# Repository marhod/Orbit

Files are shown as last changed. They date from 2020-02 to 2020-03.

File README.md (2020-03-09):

# Project Orbit, a 3D Printed Record Player

## This project is designed to be a PROOF OF CONCEPT for a 3D Printed Record Player.

### It is intended to:
* Act as a thought experiment applying modern fabrication techniques to a vintage application.
* Be a cool use of 3D Printing
* Act as a proof of concept
* Play records
* Make people say "Hey's that's cool!"
* Have some fun 3D Printing
* Maybe give some people a new lease on some crappy records from a thrift store

### It is NOT intended to do any of the following:
* Replace a manufactured turntable
* Have exceptional sound quality
* Be a perfect implementation of a design or project
* Be even a good quality turntable.  Are you kidding me?

### A quick and dirty FAQ

#### Q: This is the worst turntable ever.  You're a horrible human being.
A: ... Seriously?   It's a fricking 3D Printed record player.  If it's not cool enough, go design your own before criticising me.  When you do, ping me, because I'll tell you it's fucking awesome and want to buy you a beer.

#### Q: Why did you pick this motor?
A: I wanted something super cheap and off the shelf.  It had to be cheap, have enough torque, and be controlled with 12v.   Yes, it's noisy, but this is a proof of concept and I can source a better motor later.

#### Q: Why did you use Direct Drive?
A: I actually did the first version with belt drive, but the maths for pulley ratio and centers gets annoying when you are testing lots of different motors, which I did.

#### Q: Why did you hotglue on a cartridge?
A: This is a super cheap cartridge.  I got 3 for $10 delivered.  And frankly, using hotglue connector for this level of quality of a device is not a big deal.  Yes, it might be misaligned, but it's an experiment!  

#### Q: Why did you use a ceramic cartridge?
A: It's cheap!

#### Q: The platter wobbles.  
A: Yep it does.  I'm unsure why this happens, but my guess is it's to do with the Z axis on printers being not terribly accurate.  If it is out of plumb by even 0.1 degree that would translate to a 300mm platter wobble of 0.5 millimeter. 

#### Q: I saw the video and your beard is glorious, how can I have one?
A: Don't shave for a bit.  Then after you do that, rub it against a bee hive, ignoring the hundreds of stings from angry bees, until sufficient wax is in the beard, then mould and comb the bear into shape.  Or use product, whichever is easier.

#### Q: How can I align the cartridge?
A: Buy a better quality cartridge, then you can.  The tone arm has slots at the standard distances for a cartridge, but frankly, you have other problems that need to be solved before spending cash on a good cartridge for this device!

#### Q: How do you sleep at night?
A: On a bed filled with shattered dreams, unused parts and broken records.  But I have your mom to keep me company, so there is that...

#### Q: I saw it on Youtube and it sounds terrible 
A: It's a proof of concept made from off the shelf parts and 3D Printing.  How are you not getting this?  

## A quick note

This is a cool project and a bit of a lark.  Don't take it too seriously.

If you're looking for great sound, go spend a few thousand on a good turntable (I have).  If you're looking for a fun experiment, keep reading... :)  It's shoddily made, won't sound amazing, but I guantee your friends will say "WOAH THAT IS COOL" if you make one.  Don't put your expensive records on it, it's a fun project that may damage them.  

This project is not for beginners.  It implies a basic knowledge of electronics, arduino and sufficient skills to be able to 3D Print the parts.  All of these parts can be substituted, and hacking this to make it better is strongly encouraged.

## Parts List.

* All the STL files in this github.
* 1x 12VDc 36 RPM Geared Motor - https://www.ebay.com.au/i/254510260087?itemid=254510260087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
* 1x 2.1mm Barrel Socket - https://www.jaycar.com.au/2-1mm-bulkhead-male-dc-power-connector/p/PS0522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
* 1x 2.1mm Barrel Jack - https://www.jaycar.com.au/2-1mm-dc-power-line-connector/p/PP0509
* 1x Arduino Uno - https://www.amazon.com.au/ELEGOO-Board-ATmega328P-ATMEGA16U2-Arduino/dp/B01EWOE0UU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
* 1x Adafruit Motor Shield - https://www.adafruit.com/product/1438
* 1x Record Player Cartridge - https://www.ebay.com.au/itm/Turntable-Phono-Ceramic-Cartridge-with-Stylus-Needle-for-Vinyl-Record-Player-FS/192885929313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
* 1x 4 pack of Headshell Wires - https://www.ebay.com.au/itm/Turntable-Record-Player-Cartridge-Tonearm-Headshell-Leads-Wires-x-4-Tin-Plated/153731922565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
* 1x Illuminated Momentary Switch - https://www.ebay.com.au/itm/4-Pin-12V-12mm-Angel-Eye-LED-Light-Metal-Push-Button-Momentary-Switch-Waterproof/311981318686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
* 2x RCA Panel Mount Sockets - https://www.ebay.com.au/itm/Panel-Mount-RCA-Female-Socket-Connectors-Adapters-x-2-Pcs/273392016355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
* Thin gauge wire, a ribbon cable is perfect.
* 4x M5x16mm screw
* 1x M5x65mm Screw
* 5x M5 Nut
* 8x M3x8mm screw
* 2x M3x15/16mm screw
* 2x M3x8 Nut
* 1x M3x25mm Screw

## Basic Instruction.  I mean Basic.  Read between the lines until I publish some pictures.  This isn't instructibles.

1.  Print files.    Print the following in whatever you usually print in with PLA.  I used 10% infill and no supports or rafts.  There is one file that must be printed with 100% infill and it's clearly identified.   Choose whichever sizes you can fit on your printer, the bigger the better, but honestly, just print whatever works for you.
2.  Flash the Arduino with the .INO code provided.
3.  Attach the motor to the Motor Carrier with 2x M3x8mm screws.  Do not overtighten.  Just tight enough to be secure.
4.  Attach the Motor Carrier to the Chassis with 2x M3x8mm screws.  
5.  If you printed a two piece chassis due to a small printer, connect the two pieces with 4x M5x16mm screws and nuts.
6.  Hot glue your Cartridge (Record player needle) to the Tone Arm.
7.  Feed your thin gauge wires up through the tonearm.  
8.  Strip one end of the headshell wires, and solder the stripped end to the thin gauge wires.
9.  Connect these to the cartridge.  Take note of the pins and colors.
10.  Feed these through the hole on the chassis.
11.  Feed Attach them to the RCA jacks as per this image: https://www.turntableneedles.com/Images/CartWiring.gif
12.  Solder the 2.1mm Barrel Jack to the 2.1mm Barrel Connector with a short length of wire.
13.  Attach the Arduino with 4x M3x8mm Screws.
14.  Connect it up to the chassis, and plug the arduino into it.
15.  Time to solder the switch, do one end first, then feed it through the hole on the front of the panel, otherwise you wont be able to connect it.
16.  Thread a resistor between the - pin on the button and the GND pin on the button.
17.  Solder Pin 5 on the motor shield to the + pin on the button, using ribbon cable
18.  Solder GND on the motor shield to the - pin on the button, using ribbon cable.  
19.  Solder Pin 6 on the motor shield to one of the remaining pin that DOES NOT have a resistor., using ribbon cable.
20.  Solder GND on the motor shield to the last pin, the one that DOES have the resistor, using ribbon cable.
21.  Attach the Tone Arm Pillar to the Chassis with a M3x15mm screw.
22.  Attach the Tone Arm Bearing to the Tone Arm Pillar with a M3x8mm screw (must be loose)
23.  Attach the Tone Arm Rest to the Chassis with a M3x15mm screw.
24.  Attach the Tone Arm Rest Clip to the Tone Arm Rest with a M3x8mm screw.
25.  Attach the Hub to the Motor Spindle.  Align the flat spot with the screw hole, and insert a M3x25mm screw to act as a set screw.
26.  Push the Platter down onto the Spindle.
27.  Attach the Tone Arm to the Tone Arm Bearing using 2x M3x8mm screws (one on each side) or 1x M3x25mm screw all the way through.
28.  Plug in a 12VDC Power Supply, Sacrifice a Goat, Press the power button.
29.  Play music.

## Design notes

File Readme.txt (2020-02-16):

Print the following in whatever you usually print in with PLA.  I used 10% infill and no supports or rafts.

Hub
Motor Carrier
Tone Arm Bearing
Tone Arm Pillar
Tone Arm Rest Clip
Tone Arm Rest

Print the following in something light.  PLA is probably fine, but carbon would be cool.  You can find it in "Print in Carbon or Light Material"

Tone Arm

Print the following with 100% infill.  You can find this part in the "Print with 100% infill"

Tone Arm Weight

If you have a large volume printer (300x300mm or larger) you may be able to print the body and 300mm platter in single pieces.  These pieces can be found in "Parts for Large Build Volume".  PRINT UPSIDE DOWN FOR BEST QUALITY.

300mm Platter
Body

If you have a small volume printer (260x260mm or smaller) you will need to print these the split and smaller versions of these parts.  These can be found in the "Parts for small build volume".  Print the largest platter you can fit on your printer.    
220 / 260mm Platter
Left Hand Body
Right Hand Body

Lastly - if you want to do something cool and put a logo on the machine, I'd do it on the platter.  We could emboss it into the platter, but this may cause weight / balance issues.  A better solution would be to use a multi-material printer to paint or print it with your logo on the platter.  I don't know how to do that... :)

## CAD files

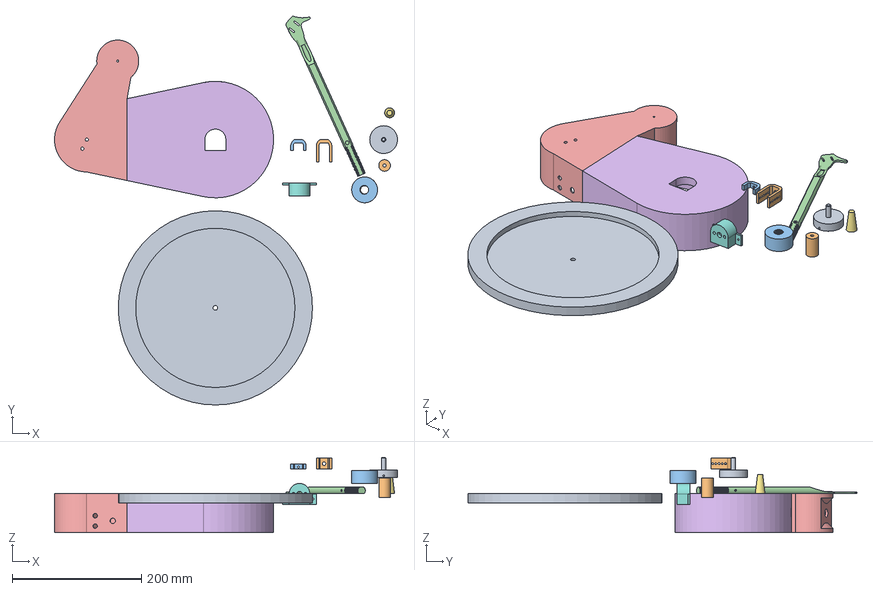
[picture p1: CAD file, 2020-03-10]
Orbit v2.step
530.0 x 600.9 x 116.0 mm

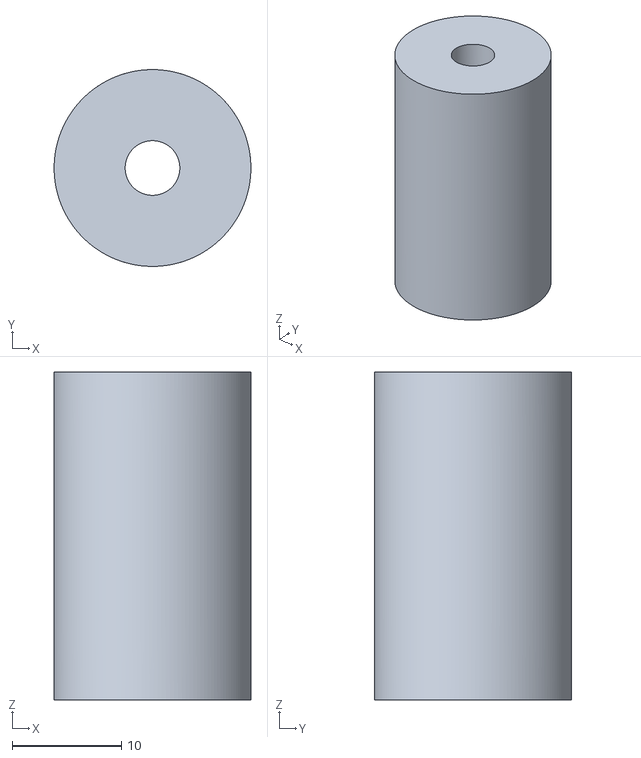
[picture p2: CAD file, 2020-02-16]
Tone Arm Pillar.stl
18.0 x 18.0 x 30.0

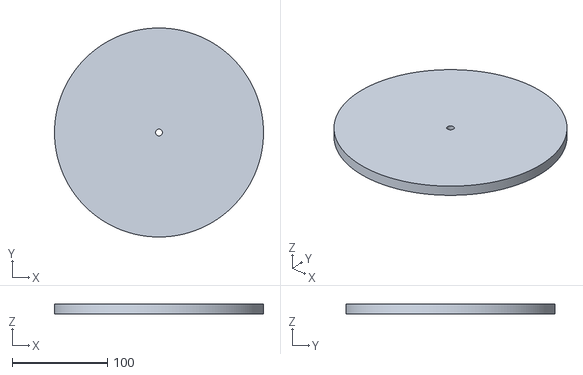
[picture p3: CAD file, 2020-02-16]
SMALL PRINTER - 220mm Platter.stl
220.0 x 220.0 x 10.0

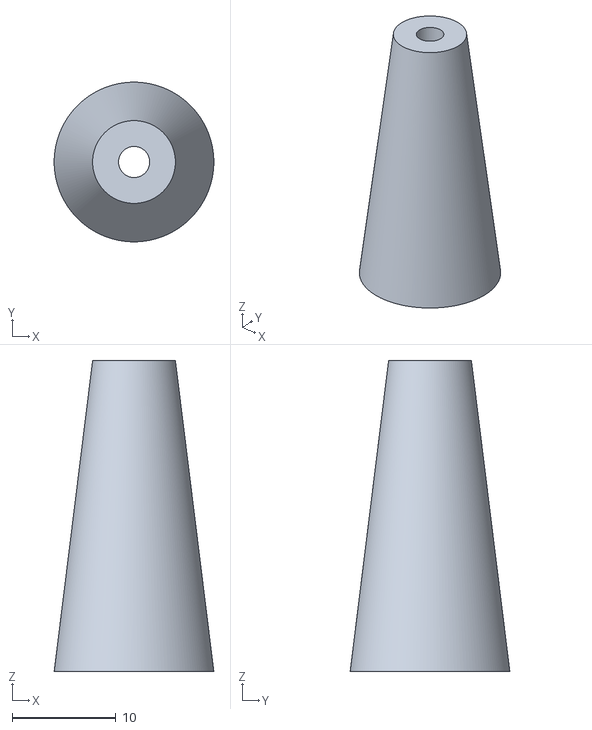
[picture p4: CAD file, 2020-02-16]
Tone Arm Rest.stl
15.4 x 15.4 x 30.0

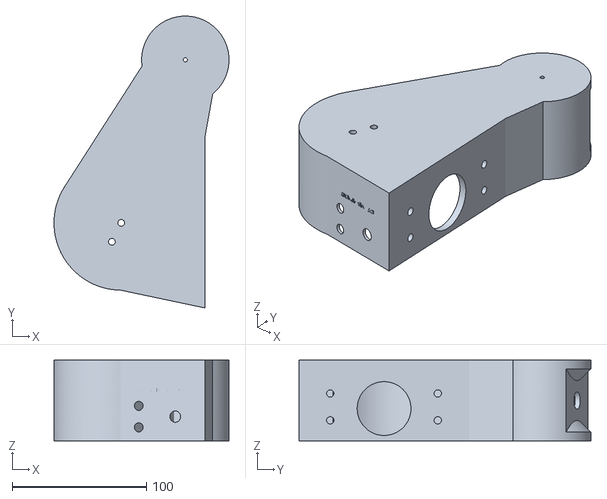
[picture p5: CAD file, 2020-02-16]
SMALL PRINTER - Chassis 1.stl
130.2 x 217.1 x 60.0

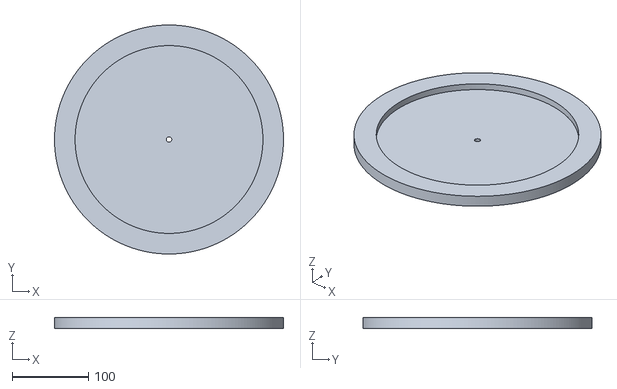
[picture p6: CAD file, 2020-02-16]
LARGE PRINTER - 300mm Platter.stl
300.0 x 300.0 x 14.0

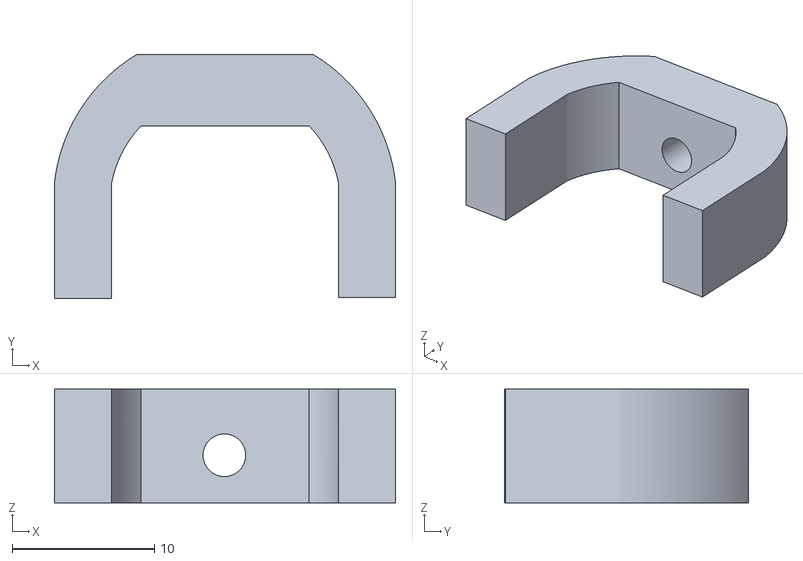
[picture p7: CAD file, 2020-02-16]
Tone Arm Rest Clip.stl
24.0 x 17.2 x 8.00

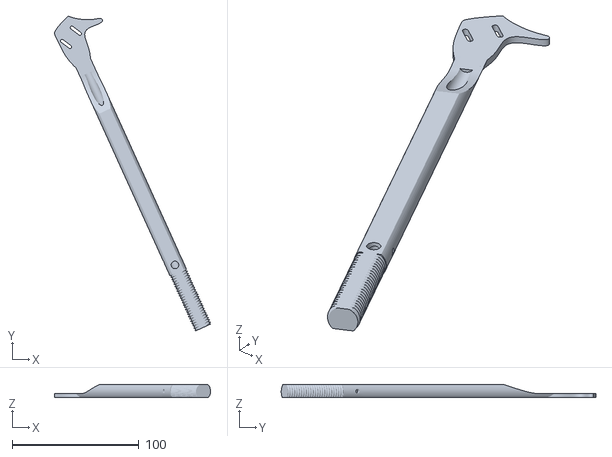
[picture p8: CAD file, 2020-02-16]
Tone Arm.stl
122.9 x 247.8 x 10.2

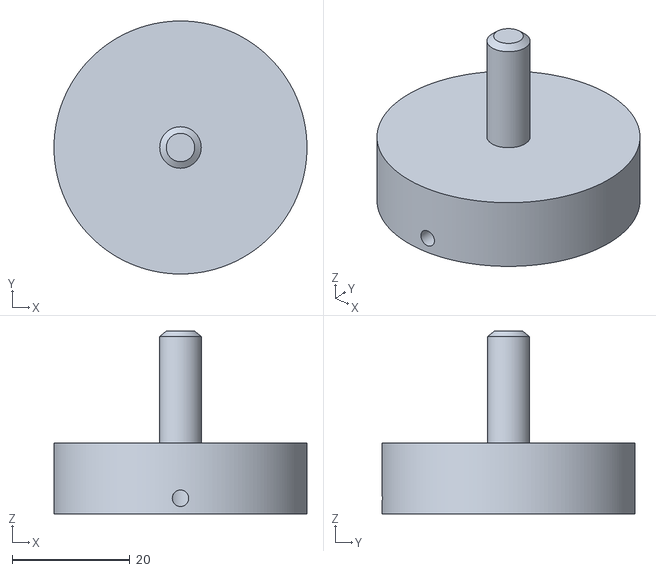
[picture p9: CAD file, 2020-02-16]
Hub.stl
42.9 x 42.9 x 31.0

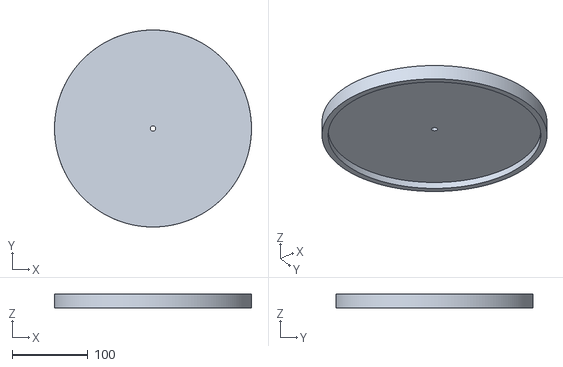
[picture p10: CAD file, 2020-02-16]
MEDIUM PRINTER - 260mm Platter.stl
260.2 x 260.2 x 18.0

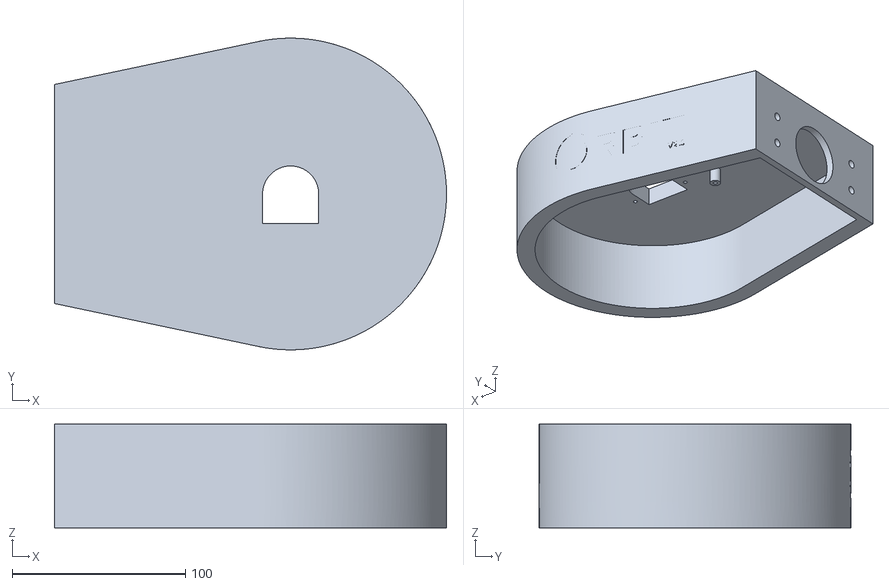
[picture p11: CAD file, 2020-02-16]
SMALL PRINTER - Chassis 2.stl
226.4 x 180.0 x 60.0

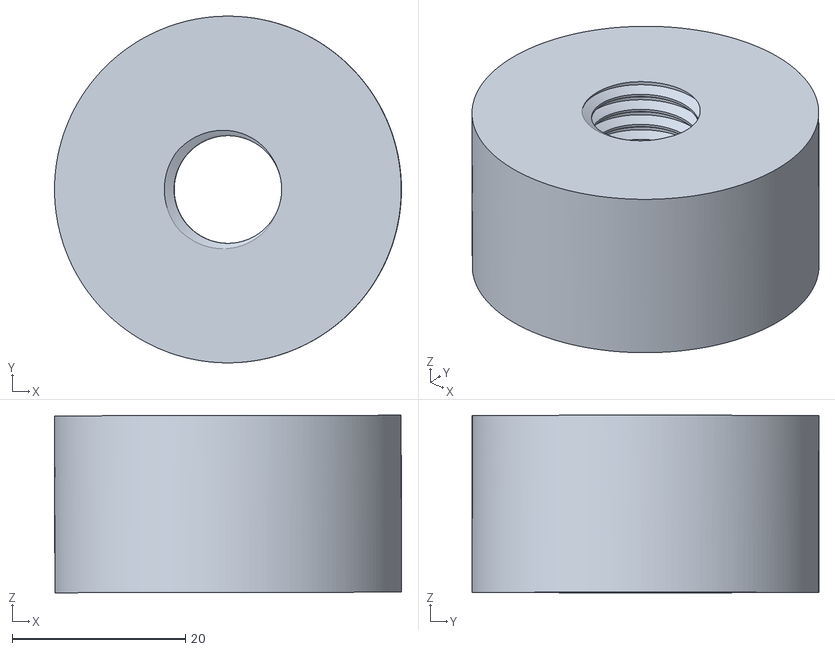
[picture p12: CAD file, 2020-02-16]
Tone Arm Weight - Print with 100% Infill.stl
40.0 x 40.0 x 20.5

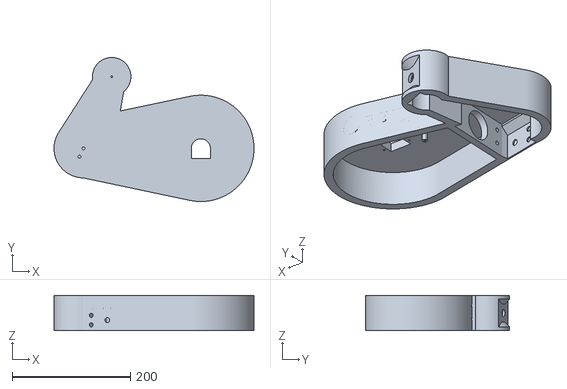
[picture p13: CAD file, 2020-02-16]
LARGE PRINTER - Chassis.stl
338.5 x 243.9 x 60.0

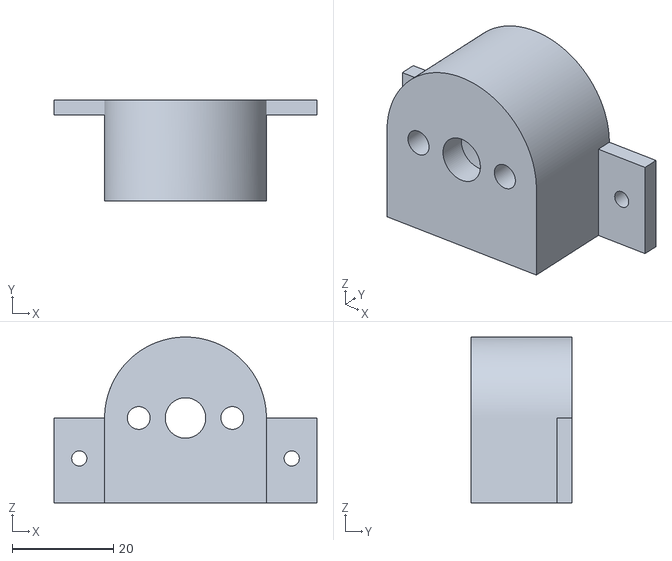
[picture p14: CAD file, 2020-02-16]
Motor Carrier.stl
52.0 x 20.0 x 32.8

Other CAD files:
Tone Arm Bearing.stl

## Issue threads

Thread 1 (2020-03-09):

CAD sources are missing

Goury, 2020-03-09:
STL is not the source and pretending it is is considered cheating.

marhod, 2020-03-09:
Agreed.  I didn't say it was...  I just use Github as a repository.   I'm
happy to make my very messy F360 timelines available if that is what you
are after?

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

Clint75, 2020-03-09:
you could make step files avalible they are easy to modify if we are allowed to.

marhod, 2020-03-10:
Done :)

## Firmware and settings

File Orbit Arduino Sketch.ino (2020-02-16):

#include <Adafruit_MotorShield.h>
Adafruit_MotorShield AFMS = Adafruit_MotorShield(); 
Adafruit_DCMotor *myMotor = AFMS.getMotor(4);

int button = 6;
int led = 5;
int state = LOW;      // the current state of the output pin
int reading;           // the current reading from the input pin
int previous = LOW;    // the previous reading from the input pin
long time = 0;         // the last time the output pin was toggled
long debounce = 200;   // the debounce time, increase if the output flickers
int spinSpeed = 250;

void setup() {
  pinMode(led,OUTPUT);
  pinMode(button,INPUT);
  AFMS.begin();
  myMotor->setSpeed(0); 
}

void loop() {
  reading = digitalRead(button);
  if (reading == HIGH && previous == LOW && millis() - time > debounce) {
    if (state == HIGH) {
      state = LOW;
      digitalWrite(led, state);
      myMotor->run(RELEASE);
    } else {
      state = HIGH;
      myMotor->run(FORWARD);
      for (int i=0; i <= spinSpeed; i=i+25){
        digitalWrite(led, LOW);
        if (i > spinSpeed) {
          myMotor->setSpeed(spinSpeed);
        } else {
          myMotor->setSpeed(i);
        }
        delay(200);
        digitalWrite(led, HIGH);
        delay(200);
      }
    }
    time = millis();    
  }
  previous = reading;
}
